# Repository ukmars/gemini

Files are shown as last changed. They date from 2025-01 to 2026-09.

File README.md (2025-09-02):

# Overview

Here is the UKMARS repository for our Gemini Micromouse. A robot capable of competing in our half size line following, Full Size Wall following and Full Size Maze Solving competitions. 

The Gemini robot is a second revision of the clubs first robot UKMARSBOT https://github.com/ukmars/ukmarsbot
Gemini has been designed so that the core microprocessor can be changed without having to change the chassis or sensor configuration. This has been done with what we call a mezzanine board. This "Mez" board connects the microprocessor to the chassis and the sensors.

At present the robot has been designed around the Raspberry Pi Pico (w)  to facilitate the use of MicroPython as a control language for the robot. This is taught is schools and allows schools to use the robot as part of their teaching aid. The Pico allows for other languages as well with the first alternative being C.

It is possible to build a Gemini robot using all commercially available parts.

In the future we hope to offer different Mez boards to allow a range of microcontrollers to be used. We are always looking for help from the community. So if you would like to design a mez board for a different microcontroller please get in touch.

This repo will contain all you need in order to build your own Gemini robot and get ready to compete in our competitions 

The groups website can be found https://ukmars.org/

A step by step build guide can currently be found https://ukmars.org/projects/gemini/

This "main" repo contains details relevant to the very latest PCB's that have been produced and distributed to schools and group members.  If you know you have a different version board than the latest (unlikely) you can find relevant KiCad documents in a release relating to your board. You will see a link to this on the right of this message

If you have found your way here without knowing about the UKMARS group, welcome. Becoming a member of UKMARS automatically gets you a set of PCB to build your own Gemini robot. All you have to do is source the parts and build.

# Technology details

All of the boards have been designed using the latest version 8 release of KiCad. They may get upgraded to version 9 but this is not a priority at the moment and the automations we have in place are not  compatible with v9.

You do not need KiCad installed in order to view the boards or the schematics

# Build details

The docs folder contains schematics, PCB renders and BOM lists. These are built directly from the KiCad and the component choices listed in the schematic represents the groups default choice of component. They are not necessarily the only option and builders are free to change the spec of components if they feel they have suitable technical knowledge to do so.
In addition to the components listed in the \docs\all_projects_bom.csv you will also need the following components to build a mouse.

# Supplier details

## Components

The following is a list of recommended UK supplier for the passive components of the board. Due to shipping costs we do recommend trying to source all passive components from one supplier if at all possible.

RSonline - https://uk.rs-online.com/web/

Rapid electronics - https://www.rapidonline.com/

Farnell - https://uk.farnell.com/

## Robot bits, Microprocessors and other

The following sites can be used to find the components not available from the above suppliers

https://thepihut.com/

https://shop.pimoroni.com/ - Motors and Encoders

https://www.amazon.co.uk/ - good for batteries and the DC motor controller

## Mechanical Parts not in the BOM

| Item | Description | part numbers and supplier options |
| --- | --- | --- |
| Encoders and encoder cables | These can be ordered along side the motor so you might have already looked at these<br>You will need two 6 pin 1mm pitch JST-SH cables to connect the motor encoder to the main board. An adaptor is used to convert the JST-SH cable to 2.54 pitch to connect it to J1 and J2 | |
| Encoder adapter board | This board converts JST-SH to 2.54 pins.<br>This does make soldering of the robot easier.<br>You can omit this part if you are comfortable soldering wires from a JST-SH cable direct to the chassis board | https://thepihut.com/products/breakout-for-6-pin-jst-sh-style-connector-side-entry |
| JST_SH cables | These cables connect the motor encoder to the chassis.<br><br>If you are comfortable soldering small cables direct to the chassis then you can use the second option. You DO NOT need the JST-SH adaptor board if you solder the wires direct to the chassis. This option is for experienced builders only as it increases the risk of problems with motors and/or encoders reading being reversed.  | https://thepihut.com/products/jst-gh-1-25mm-pitch-6-pin-cable-100mm-long<br><br><br>https://amzn.eu/d/hsau12j |
| Wheels and Tyres | Pololu Wheel 32×7mm Pair available in black or white or you could 3D print some and use O rings for tyres | Pi Hut SKU: POL-1087 or SKU: POL-1088<br><br>https://thepihut.com/products/pololu-wheel-32x7mm-pair-black |
| Motor Mounts | You need 2 motor mounts. They can be 3D printed if you have the capability or you can buy the Polulo ones.<br><br>3D print models can be found in the \mechanical folder. GeminiN20MotorMount.STL - Print upside down | Pi Hut code SKU: POL-989<br><br>https://thepihut.com/products/pololu-micro-metal-gearmotor-bracket-pair-black |
| Battery and connector | The battery should be a PP3 9Volt block Lithium Ion rechargeable one with micro USB charging socket and ideally charge level LEDs on the side.<br>Ideally 1200mAH capacity or greater | https://amzn.eu/d/i8hoP5S<br><br>https://amzn.eu/d/cmckSHt<br><br>Rapid Online Order Code: 18-0092 |
| Nuts and bolts | If you are using 3D printed mounts which have 3mm holes in them you need 4 M3 x 30mm flat head polyamide bolts. Pack of M3 polyamide nuts 8 required<br><br>M3 x 10mm plastic spacers or 10mm piece of plastic tubing<br><br>Ebay is a good place to order small quantities of M3 hardware | Rapid Online Order Code: 51-3852<br><br>Rapid-Online Order Code: 51-3437<br><br>https://www.ebay.co.uk/str/kaysfasteners<br><br> |
| Stand Offs | Used for mounting connecting the sensor and mez board to the chassis<br><br>Lots of ways to do this but a pack of standoff's makes this simple.<br><br>A nylon screw and nut can be used as a skid | https://amzn.eu/d/eMlVNY3<br><br> |
|Screen|Not required, but a screen can be helpful. The important thing with a screen is the pin order which needs to be Gnd, Vcc, SCL, SDA left to right. Other screens can be used but will require custom connectors <br> *Warning* The screens available from Pimoroni can be used but their GND and Vcc pins are reversed when compared to the mez board connector. EXTREME care needs to be taken if wiring these|https://a.aliexpress.com/_EJEPBEO <br> https://amzn.eu/d/ffaTN75 

> All of the options here are what UKMARS believe to be the best starting options for schools and new builders. It does not represent the only options available. If you have suitable experience and knowledge feel free to swap components as you see fit. If you do deviate from the build guide and/or suggested components please make sure to mention this if you encounter problems.

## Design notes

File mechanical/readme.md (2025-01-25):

# Project Gemini - Mechanical Design

Here you will find parts models, drawings and descriptions relating ot the mechanical design of the Gemni robot.

This covers the physical layout and arrangement of the major components including the PCBs that make up the main chassis, the processor carrier, sensor boards, drive components and battery.

Something like this perhaps -though with less wood.

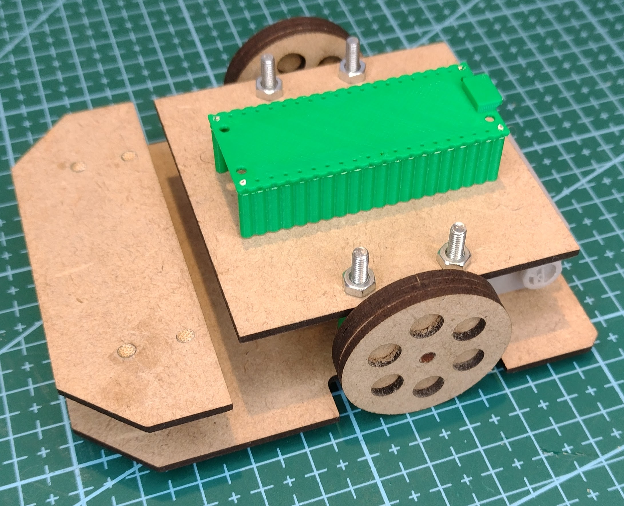
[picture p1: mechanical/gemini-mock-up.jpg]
gemini


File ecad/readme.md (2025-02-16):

# ECAD

Here you will find ECAD design files and resources such as part and footprint libraries.

The project will use KiCAD V8.0.x for all Schematic capture and PCB design.

Part datasheets will be stored in a separate folder.

Kicad models for the pico where found [here](https://github.com/ncarandini/KiCad-RP-Pico)
Install instructions [here](https://github.com/ncarandini/KiCad-RP-Pico/blob/main/Install%20instructions.md)

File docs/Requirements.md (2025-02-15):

# Requirements and Design Choices for Gemini

## Brief

This document states the core requirements and end offering that Gemini will provide.

## Board connections

| Name | Pin  | A/D | Direction | Function |
|---|---|-----|---|---|
| **Connector 1 on Chassis to Mezzanine** |  |  |  |  |
| 5v | Con1 | 0 | Pwr Out | +5v regulated supply provided by chassis |
| Gnd | Con1 | 1 | Pwr Out | Gnd provided by chassis |
| LMTR1 | Con1 | 2 D | In | Left motor input 1 to bridge |
| LMTR2 | Con1 | 3 D | In | Left motor input 2 to bridge |
| RMTR1 | Con1 | 4 D | In | Right motor input 1 to bridge |
| RMTR2 | Con1 | 5 D | In | Right motor input 2 to bridge |
| **Connector 2 on Chassis to Mezzanine** |  |  |  |  |
| LQA | Con2 | 0 D | Out | Left quadrature encoder channel A |
| LQB | Con2 | 1 D | Out | Left quadrature encoder channel B |
| RQA | Con2 | 2 D | Out | Right quadrature encoder channel A |
| RQB | Con2 | 3 D | Out | Right quadrature encoder channel B |
| 3v3 | Con2 | 4 A | Pwr In | 3V3 regulated supply provided by mezzanine |
| Vbatt | Con2 | 5 A | Pwr Out | Battery voltage supply after polarity protection |
| **Connector 3 on Mezzanine to Sensor Board** |  |  |  |  |
| Vemit | Con3 | 0 | Pwr Out | Power supply for sensor emitters, designers choice from 5v, Vbatt or 3v3 |
| Gnd | Con3 | 1 | Pwr Out | Gnd routed from chassis |
| 3v3 | Con3 | 4 | Pwr Out | 3V3 regulated supply provided by mezzanine |
| SEN0DIO | Con3 | 5 D | In/Out | Digital I/O line 0 for sensors |
| SEN1DIO | Con3 | 6 D | In/Out | Digital I/O line 1 for sensors |
| SEN2DIO | Con3 | 7 D | In/Out | Digital I/O line 2 for sensors |
| SEN3DIO | Con3 | 8 D | In/Out | Digital I/O line 3 for sensors |
| SEN4DIO | Con3 | 9 D | In/Out | Digital I/O line 4 for sensors |
| SEN0AIP | Con3 | 10 A | In | Analogue input for sensor 0 |
| SEN1AIP | Con3 | 11 A | In | Analogue input for sensor 1 |
| SEN2AIP | Con3 | 12 A | In | Analogue input for sensor 2 |
| SEN3AIP | Con3 | 13 A | In | Analogue input for sensor 3 |
| SEN4AIP | Con3 | 14 A | In | Analogue input for sensor 4 |
| SEN5AIP | Con3 | 15 A | In | Analogue input for sensor 5 |
| SDA | Con3 | 14 D | In/Out | I2C Serial Data |
| SCL | Con3 | 15 D | In/Out | I2C Serial Clock |

## Main board

Will be the same size and dimensions of UKMARSBOT

## Processor Support

The primary Processor with be the Raspberry Pi RP2040, other processors can be supported with additional mezanine boards, the development of these boards is for robot builders to pursue.

## Mezzanine boards

Initially we will be designing a Mezzanine board for the PiPico/PiPicoW

Meazanine boards will achieve connection with the main chassis board with 20mm extented male headers. 0ptionally stackable female headers from the chassis board can be used with standard male headers on the mezanine board.
The mezanine board will be mounted on the rearmost pair of motor bracket bolts and the rearmost pair of sensor mounting bolts.
## Sensors

### Wall Sensor

### Line Sensor

## Motors

N20 extended motor shaft DC motors with side mount encoders. Gear ratios to be selected by the builder. Recommended ratios 50:1, 30:1 or 20:1. Higher ratios give better resolution and easier control, lower ratios give highr top speed.

[Motor and Encoders](https://shop.pimoroni.com/products/micro-metal-motor-encoder?variant=39888423354451)
or 
https://shop.pimoroni.com/products/micro-metal-motor-encoder?variant=39888423354451

The above encoders are preferred as they can route the cable forwards without adding height to the motor assembly. Other encoders with cables emerging at the top may fit withing the headroom above the motor, builders will need to confirm this if choosing alternative encoders.
The connection to the encoders are JST-SH, if possible pads for corresponding JST-SH sockets will be included in the chassis board. 0.1inch x 6 connectors will be included on the chassis board. 

## Motor Controller
We have decided to use the DRV8833 chipset on a Switch/HW-627 module board which available from multiple suppliers on Amazon or eBay.
Example supplier (no recommendation) https://www.ebay.co.uk/itm/285548428267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
Example supplier (no recommendation) https://www.ebay.co.uk/itm/195060438441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

Found [here](https://www.amazon.co.uk/dp/B07ML2RDNY) as well

Nice article explaining how to wire up [drv8833-arduino-tutorial](https://lastminuteengineers.com/drv8833-arduino-tutorial/)

## Motor Mounts
Pololu motor mounts or equivalent can be used. 3d Printed mounts will offer a better solution using standard M3 or M2.5 bolts with standoffs to mount the mezanine board.

## Wheels and Tyres
Standard 32mm Pololu wheels and tyres or equivalents will be used https://thepihut.com/products/pololu-wheel-32x7mm-pair-black

## Batteries

The design will accommodate a PP3 battery form factor. Builders may use any PP3 battery they prefer, or any other battery that will fit withing the form factor of a PP3 battery and presents a voltage no greater than 9v.
The battery connection to the chassis board will be 0.1inch x2. A polarised connector can be used but is not mandatory so a polarity protection diode is required on the chassis board.

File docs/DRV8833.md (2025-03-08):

# The DRV8833 Motor Driver

The chosen driver carrier is commonly available. It loks like this:



## SLEEP input

The driver chip has a pin called nSLEEP. On these cheap carriers, that pin is connected to a pin usually called 'EEP'. I guess they ran out of space.

From the perspective of the driver chip, if this pin is left open, it is pulled down by an internal resistor and the chip will be in sleep mode. That is, you will not get any outputs to the motors.

To enable the driver, the nSLEEP pin must be pulled up to the motor Voltage, $V_M$.

BUT...

There are many version of  the carrier. They have slightly different markings and they may, or may not, pull up the nSLEEP pin. This picture, from a random AliExpress vendor shows a jumper on the rear. It clearly shows hat the jumper must be bridged to enable the outputs. There is a 47k resisor on the board that performs this function when the jumper is bridged.


Apparently though, there are boards that have this jumper already bridged on the board so the outputs are always active.

Note that, if you look at boards from Pololu and Adafruit, this pin may, or may not already be pulled high. The Pololu carrier puls it high, the Adafruit carrier does not:

 - Pololu: https://www.pololu.com/product/2130
 - Adafruit: https://learn.adafruit.com/assets/36870

To be sure  the motor drive is enabled, pull the nSleep ('EEP) pin high with a 47k resistor connected to the motor supply.

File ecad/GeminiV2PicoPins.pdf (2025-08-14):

## UKMARS Gemini V2 PiPico Pin assignements

### Chassis and Mezzanine Pins

Pico GPIO | Mezz Net ID | Used on | Device | Device name | Description
| 0 GPIO00 | Mezz | J2-2 | Breakout connector | UART0-TX for bluetooth or GPIO pin
| 1 GPIO01 | Mezz | J2-3 | Breakout connector | UART0-RX for bluetooth or GPIO pin
| 2 LMTR1 | Chassis | U1-7 | DRV8833 motor controller | Left motor control signal 1
| 3 LMTR2 | Chassis | U1-8 | DRV8833 motor controller | Left motor control signal 2
| 4 RMTR1 | Chassis | U1-11 | DRV8833 motor controller | Right motor control signal 1
| 5 RMTR2 | Chassis | U1-12 | DRV8833 motor controller | Right motor control signal 2
| 6 RQA | Chassis | J2-3 | Right motor quadrature encoder | Signal A
| 7 RQB | Chassis | J2-2 | Right motor quadrature encoder | Signal B
| 8 LQA | Chassis | J1-3 | Left motor quadrature encoder | Signal A
| 9 LQB | Chassis | J2-2 | Left motor quadrature encoder | Signal B
| 10 GPIO10 | Mezz | J5-4 | Breakout connector | I2C1-SDA for display or GPIO pin
| 11 GPIO11 | Mezz | J5-3 | Breakout connector | I2C1-SCL for display or GPIO pin
| 12 GPIO12 | Mezz | D1 | Indicator LED | Left side
| 13 GPIO13 | Mezz | D2 | Indicator LED | Right side
| 14 GPIO14 | Mezz | SW2 | Pushbutton | Right side
| 15 GPIO15 | Mezz | SW1 | Pushbutton | Left side

### Line Sensor Pins

Pico GPIO | Mezz Net ID | Used on | Device | Device name | Description
| 16 SDA | Line Sensor | Not used
| 17 SCL | Line Sensor | Not used
| 18 SEN4DIO | Line Sensor | Q6 | BC337-40 | Radius emitter driver
| 19 SEN3DIO | Line Sensor | D6 | Indicator LED | S/F right side indicator
| 20 SEN2DIO | Line Sensor | D5 | Indicator LED | Line central indicator
| 21 SEN1DIO | Line Sensor | D4 | Indicator LED | Radius left side indicator
| 22 SEN0DIO | Line Sensor | Q1 | BC337-40 | Line and start/finish emitter driver
| 26 SEN2AIP | Line Sensor | Q4 | BPW85C | Line right side detector
| 27 SEN1AIP | Line Sensor | Q2 and Q5 | BPW85C | Radius and Start/finish detectors
| 28 SEN0AIP | Line Sensor | Q3 | BPW85C | Line left side detector
Not available | SEN3AIP | Not available
Not available | SEN4AIP | Not available
Not available | SEN5AIP | Not available

Page 1 of 2

### Wall Sensor Pins

Pico GPIO | Mezz Net ID | Used on | Device | Device name | Description
| 16 SDA | Wall Sensor | Not used
| 17 SCL | Wall Sensor | Not used
| 18 SEN4DIO | Wall Sensor | D3 | Indicator LED | Right side indicator
| 19 SEN3DIO | Wall Sensor | D2 | Indicator LED | Central (to the right) indicator
| 20 SEN2DIO | Wall Sensor | D1 | Indicator LED | Left side indicator
| 21 SEN1DIO | Wall Sensor | Q2 | BC337-40 | Driver for diagonal emitters
| 22 SEN0DIO | Wall Sensor | Q1 | BC337-40 | Driver for front emitter
| 26 SEN2AIP | Wall Sensor | RDPD1 | BPW85C | Right diagonal detector
| 27 SEN1AIP | Wall Sensor | FPD1 | BPW85C | Front detector
| 28 SEN0AIP | Wall Sensor | LDPD1 | BPW85C | Right diagonal detector
Not available | SEN3AIP | Not available
Not available | SEN4AIP | Not available
Not available | SEN5AIP | Not available

Page 2 of 2

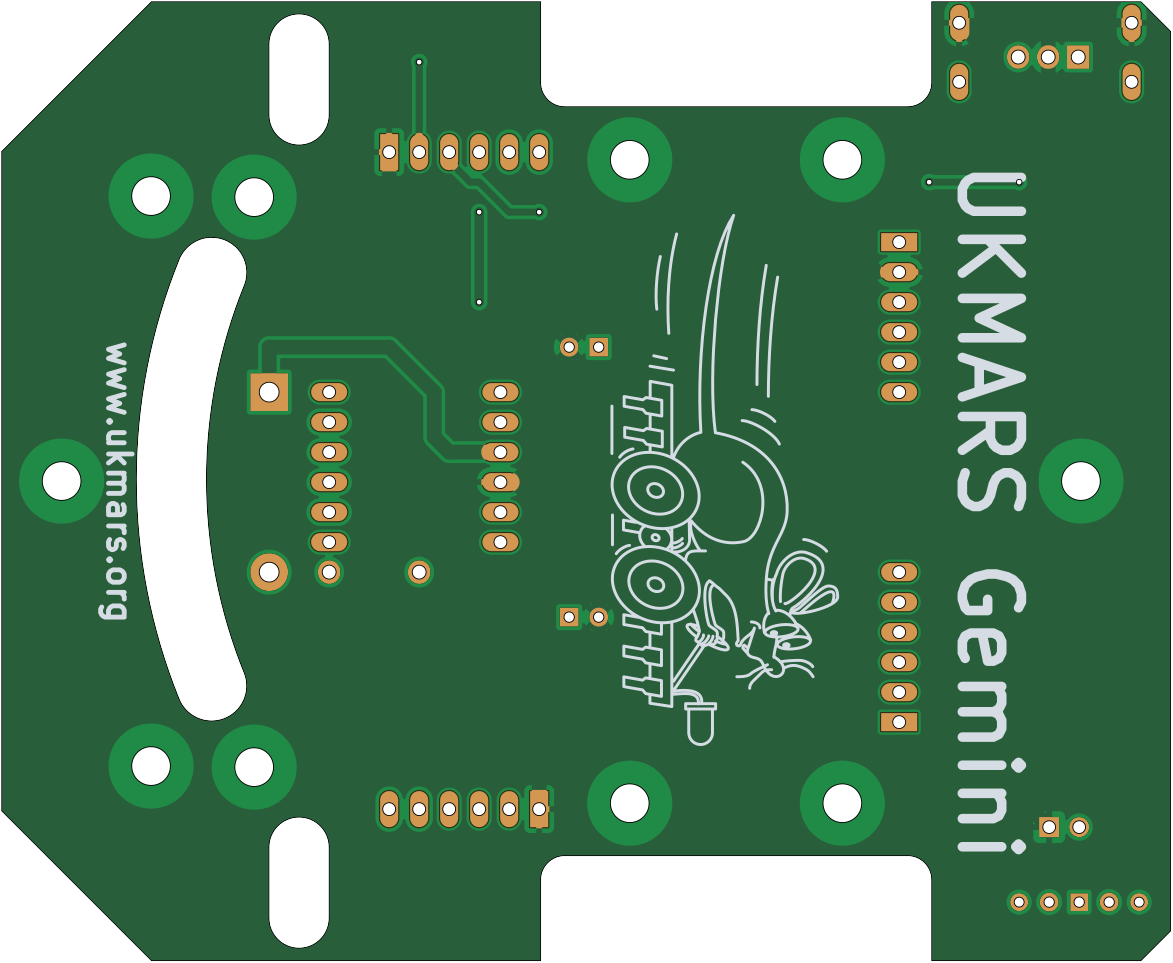
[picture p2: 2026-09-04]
docs/UKMARSBOT_RP2040Chassis/UKMARSBOT_RP2040Chassis_board_bottom.png

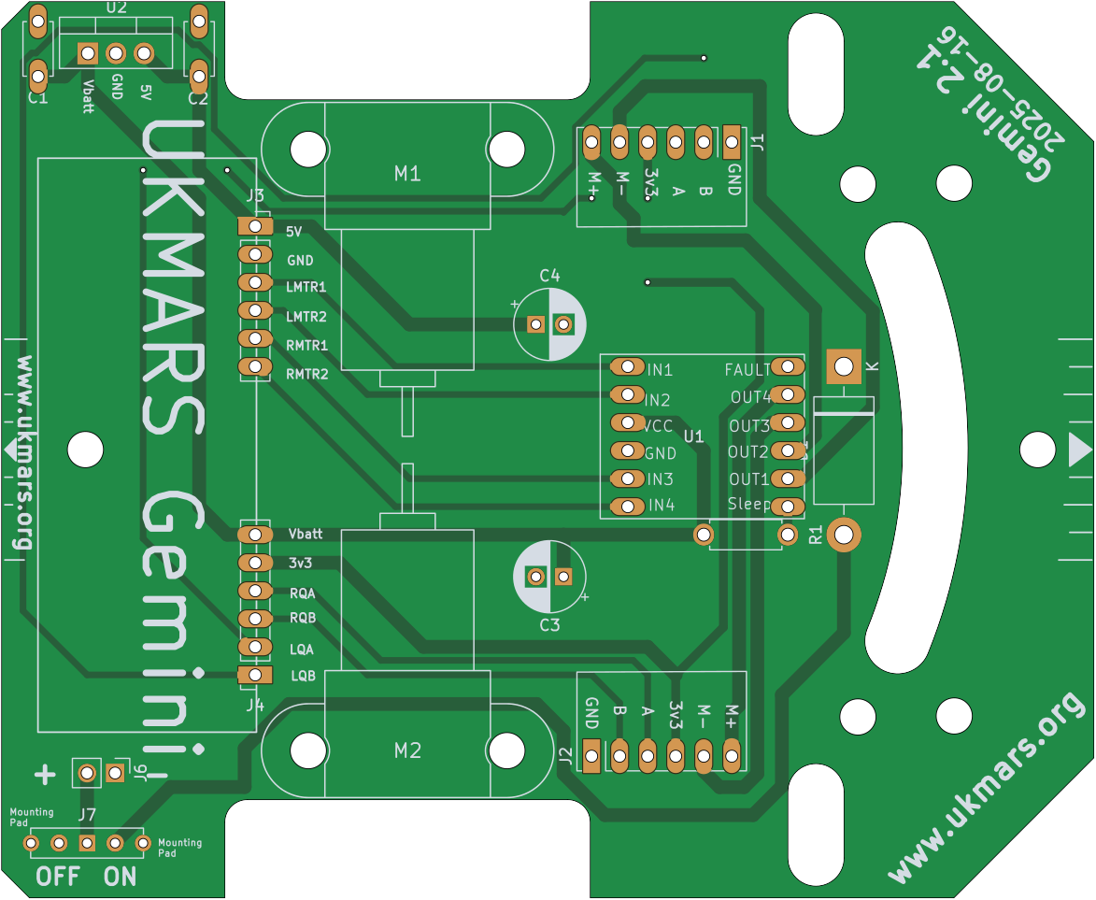
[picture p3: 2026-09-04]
docs/UKMARSBOT_RP2040Chassis/UKMARSBOT_RP2040Chassis_board_top.png

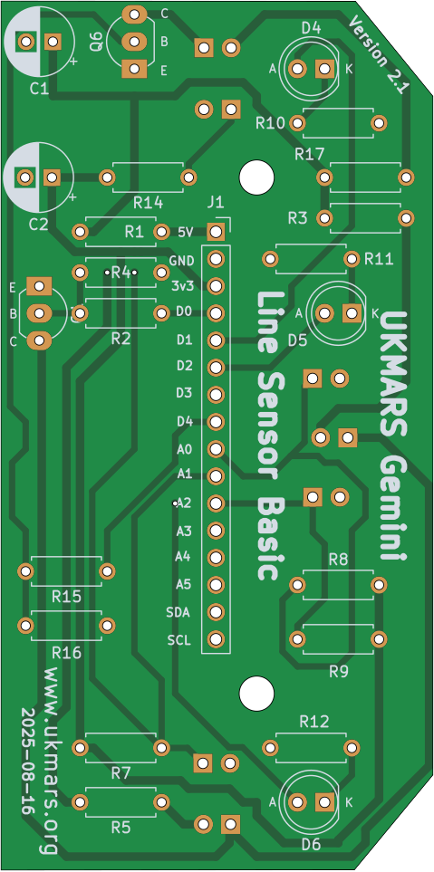
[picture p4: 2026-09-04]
docs/UKMARSBOT_LineSensorBasic/UKMARSBOT_LineSensorBasic_board_top.png

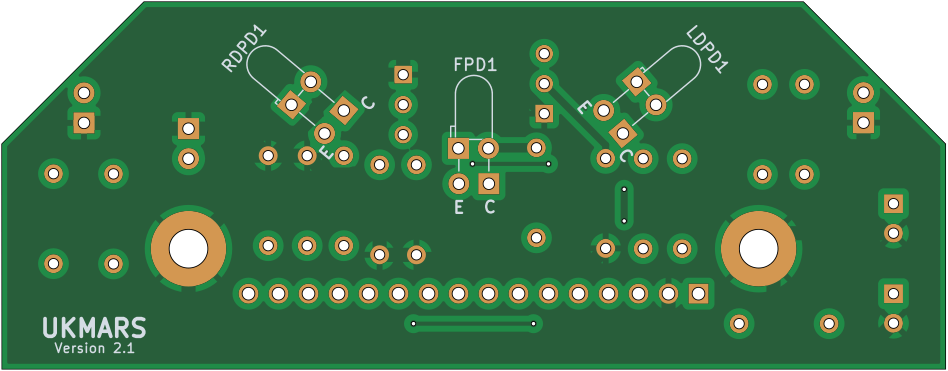
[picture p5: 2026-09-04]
docs/UKMARSBOT_RP2040Wall-Sensor-Basic/UKMARSBOT_RP2040Wall-Sensor-Basic_board_bottom.png

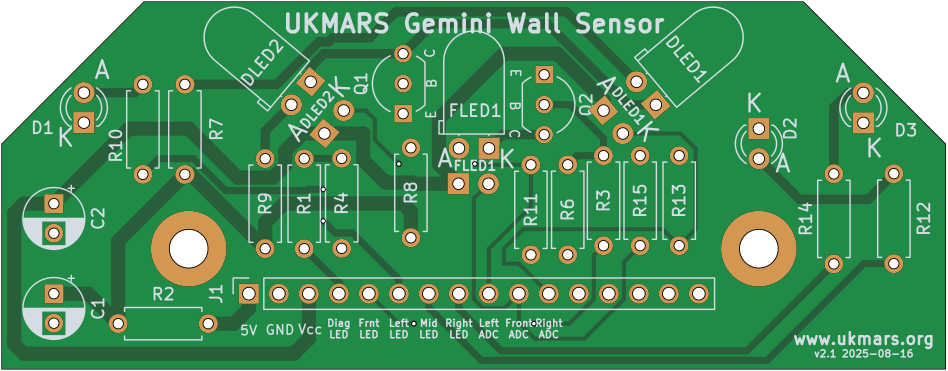
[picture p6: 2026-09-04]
docs/UKMARSBOT_RP2040Wall-Sensor-Basic/UKMARSBOT_RP2040Wall-Sensor-Basic_board_top.png

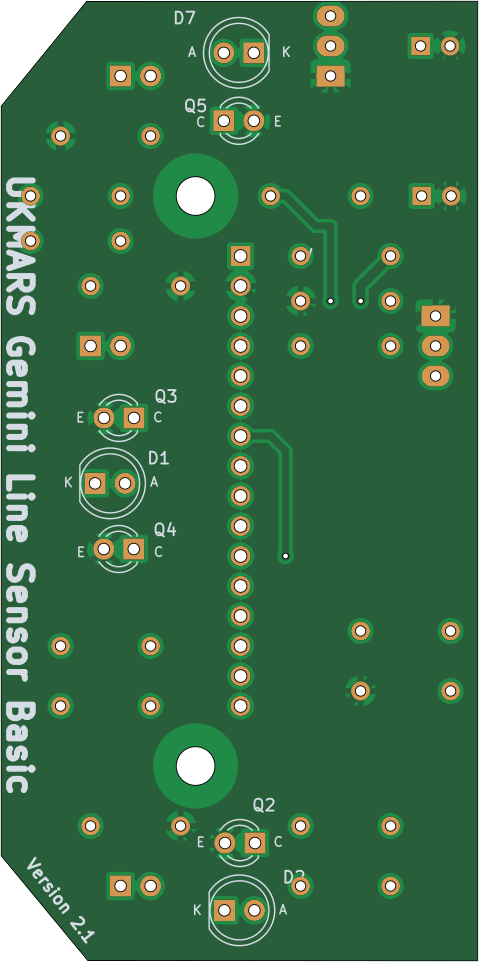
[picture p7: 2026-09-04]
docs/UKMARSBOT_LineSensorBasic/UKMARSBOT_LineSensorBasic_board_bottom.png

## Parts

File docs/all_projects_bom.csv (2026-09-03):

Project | Reference | Value | Qty | Note | Description | RSONLINE | RAPID
UKMARSBOT_LineSensorBasic | C1 C2 | 100uF | 2 |  | Polarized capacitor | 176-3779 | 11-4109
UKMARSBOT_LineSensorBasic | D1 D2 D7 | TLCR5800 | 3 |  |  | 818-7540 | 55-0066
UKMARSBOT_LineSensorBasic | D4 | Radius | 1 |  |  | "228-6004 or 228-5562 or 713-3974 or 813-4845" | 56-0400
UKMARSBOT_LineSensorBasic | D5 | Line | 1 |  |  | "228-6004 or 228-5562 or 713-3974 or 813-4845" | 56-0405
UKMARSBOT_LineSensorBasic | D6 | S/Finish | 1 |  |  | "228-6004 or 228-5562 or 713-3974 or 813-4845" | 56-0410
UKMARSBOT_LineSensorBasic | J1 | Conn_01x16 | 1 | https://uk.rs-online.com/web/p/pcb-sockets/6816820 Need to be cut down | Generic connector, single row, 01x16, script generated (kicad-library-utils/schlib/autogen/connector/) | 681-6820 | 19-0087
UKMARSBOT_LineSensorBasic | Q1 Q6 | BC337-40 | 2 |  |  | 671-1119 | 50-3113
UKMARSBOT_LineSensorBasic | Q2 Q3 Q4 Q5 | BPW85C | 4 |  |  | 815-1263
UKMARSBOT_LineSensorBasic | R1 | 47R | 1 |  | Resistor | 707-8817 | 62-0334
UKMARSBOT_LineSensorBasic | R2 R15 | 390R | 2 |  |  | 707-7634 | 62-0360
UKMARSBOT_LineSensorBasic | R3 R5 R17 | 10R | 3 |  |  | 707-8580 | 62-0326
UKMARSBOT_LineSensorBasic | R4 R16 | 10K | 2 |  |  | 707-7745 | 62-0394
UKMARSBOT_LineSensorBasic | R7 R8 R9 R10 R11 R12 R14 | 680R | 7 |  |  | 707-8211 | 64-0068
UKMARSBOT_RP2040Chassis | BT1 | 9v Battery | 1 |  | PP3 9v Battery
UKMARSBOT_RP2040Chassis | C1 | 0.22uF | 1 | Maximum height is 10mm | Unpolarized capacitor | 194-0629 | 11-3449
UKMARSBOT_RP2040Chassis | C2 | 0.1uF | 1 | Maximum height is 10mm | Unpolarized capacitor | 538-1433 | 11-3442
UKMARSBOT_RP2040Chassis | C3 C4 | 100uF, 16V | 2 | Maximum height is 10mm |  | 176-3779 176-3779 | 11-4109
UKMARSBOT_RP2040Chassis | D1 | 1N5401 | 1 | Polarity protection diode |  | 628-9451
UKMARSBOT_RP2040Chassis | J1 J2 | Pololu Item #4772 | 2 | 6 pin 0.1" breakout 6 pin header, 0.1", male | Single row, 01x06, JST-SH breakout |  | 22-0795
UKMARSBOT_RP2040Chassis | J3 J4 J6 J7 | Conn_01x06 | 4 | Might be easier and cheaper to just cut from bigger lengths 0.1" pitch, polarised, any type | https://uk.rs-online.com/web/p/pcb-headers/6812994 | 681-2994 | 01-5723 08-5765 78-0566
UKMARSBOT_RP2040Chassis | M1 M2 | N20 MOTOR | 2 | Sidways or regular would work for starting out 50:1 gearbox is recommended commercial mounts need bushing for screws | https://shop.pimoroni.com/products/micro-metal-motor-encoder?variant=39888423321683 | NA
UKMARSBOT_RP2040Chassis | R1 | 47K | 1 |  | Resistor | 707-8369 | 62-0410
UKMARSBOT_RP2040Chassis | U1 | DVR8833_DC_Controller | 1 |  | DC Motor Controller https://amzn.eu/d/csv7cRr as an option
UKMARSBOT_RP2040Chassis | U2 | LM7805_TO220 | 1 |  | Positive 1A 35V Linear Regulator, Fixed Output 5V, TO-220 | 793-1346
UKMARSBOT_RP2040Mezzanine | D1 D2 | LED | 2 |  | Light emitting diode | "228-6004 or 228-5562 or 713-3974 or 813-4845" | 56-0400 and 56-0405
UKMARSBOT_RP2040Mezzanine | J1 J2 J3 J4 J5 | Conn_01x16 | 5 | Might be easier and cheaper to just cut from bigger lengths Cut from a bigger strip of 2.54 header | Generic connector, single row, 01x16, script generated (kicad-library-utils/schlib/autogen/connector/) Generic connector, single row, 01x06, script generated (kicad-library-utils/schlib/autogen/connector/) Generic connector, single row, 01x04, script generated | 681-3007 681-2994 | 08-7948 01-5723 01-5835
UKMARSBOT_RP2040Mezzanine | R1 R2 | 680R | 2 |  | Resistor | 707-8211 | 64-0068
UKMARSBOT_RP2040Mezzanine | SW1 SW2 SW3 | TACT_SW | 3 |  | TACT switch 6mm 4.5mm | 479-1390P | 78-3821
UKMARSBOT_RP2040Mezzanine | U1 | Pico | 1 |  |  |  | 08-7949 and 75-1230
UKMARSBOT_RP2040Wall-Sensor-Basic | C1 C2 | 100uF, 16v | 2 |  | Unpolarized capacitor | 739-6799 | 11-4119
UKMARSBOT_RP2040Wall-Sensor-Basic | D1 D2 D3 | LED | 3 |  | Light emitting diode | "228-6004 or 228-5562 or 713-3974 or 813-4845" | 56-0400 or 56-0405 or 56-0410
UKMARSBOT_RP2040Wall-Sensor-Basic | DLED1 DLED2 FLED1 | TLCR5800 | 3 |  | Light emitting diode | 818-7540
UKMARSBOT_RP2040Wall-Sensor-Basic | FPD1 LDPD1 RDPD1 | BPW85C | 3 |  | Photodiode | 815-1263
UKMARSBOT_RP2040Wall-Sensor-Basic | J1 | Conn_01x16 | 1 | https://uk.rs-online.com/web/p/pcb-sockets/6816820 Can also be found on ebay slightly cheaper | Generic connector, single row, 01x16, script generated (kicad-library-utils/schlib/autogen/connector/) | 681-6820 | 19-0087
UKMARSBOT_RP2040Wall-Sensor-Basic | Q1 Q2 | BC337-40 | 2 |  | NPN transistor, emitter/base/collector | 671-1119 | 50-3113
UKMARSBOT_RP2040Wall-Sensor-Basic | R1 R3 | 390R | 2 |  | Resistor | 707-7634 | 62-0360
UKMARSBOT_RP2040Wall-Sensor-Basic | R10 R12 R14 | 680R | 3 |  | Resistor | 707-8211
UKMARSBOT_RP2040Wall-Sensor-Basic | R11 R13 | 2k2 | 2 |  | Resistor | 707-8255 | 62-0378
UKMARSBOT_RP2040Wall-Sensor-Basic | R15 | 1k8 | 1 |  | Resistor | 707-8675 | 62-0376
UKMARSBOT_RP2040Wall-Sensor-Basic | R2 | 33R | 1 |  | Resistor | 707-8805 | 62-0334
UKMARSBOT_RP2040Wall-Sensor-Basic | R4 R6 | 10K | 2 |  | Resistor | 707-7745 | 62-0394
UKMARSBOT_RP2040Wall-Sensor-Basic | R7 R8 R9 | 10R | 3 |  | Resistor | 707-8580 | 62-0326

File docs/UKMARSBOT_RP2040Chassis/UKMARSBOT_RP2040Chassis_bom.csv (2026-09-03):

Reference | Value | Qty | Note | Description | RSONLINE | RAPID
BT1 | 9v Battery | 1 |  | PP3 9v Battery
C2 | 0.1uF | 1 | Maximum height is 10mm | Unpolarized capacitor | 538-1433 | 11-3442
C1 | 0.22uF | 1 | Maximum height is 10mm | Unpolarized capacitor | 194-0629 | 11-3449
C3 C4 | 100uF, 16V | 2 | Maximum height is 10mm |  | 176-3779 176-3779 | 11-4109
D1 | 1N5401 | 1 | Polarity protection diode |  | 628-9451
J3 J4 J6 J7 | Conn_01x06 | 4 | Might be easier and cheaper to just cut from bigger lengths 0.1" pitch, polarised, any type | https://uk.rs-online.com/web/p/pcb-headers/6812994 | 681-2994 | 01-5723 08-5765 78-0566
J1 J2 | Pololu Item #4772 | 2 | 6 pin 0.1" breakout 6 pin header, 0.1", male | Single row, 01x06, JST-SH breakout |  | 22-0795
M1 M2 | N20 MOTOR | 2 | Sidways or regular would work for starting out 50:1 gearbox is recommended commercial mounts need bushing for screws | https://shop.pimoroni.com/products/micro-metal-motor-encoder?variant=39888423321683 | NA
R1 | 47K | 1 |  | Resistor | 707-8369 | 62-0410
U1 | DVR8833_DC_Controller | 1 |  | DC Motor Controller https://amzn.eu/d/csv7cRr as an option
U2 | LM7805_TO220 | 1 |  | Positive 1A 35V Linear Regulator, Fixed Output 5V, TO-220 | 793-1346

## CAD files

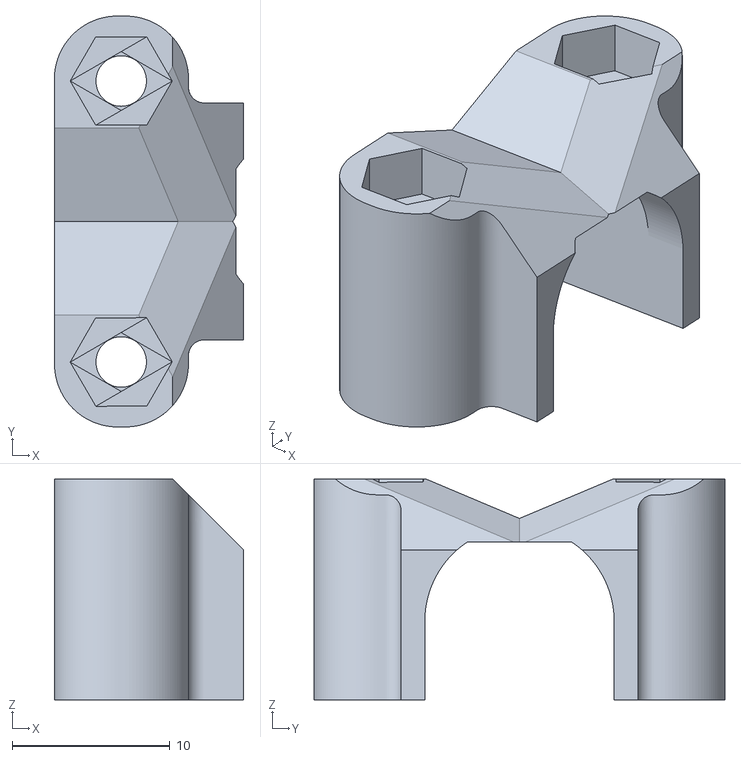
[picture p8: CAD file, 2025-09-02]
mechanical/GeminiN20MotorMount.stl
12.0 x 26.0 x 14.0

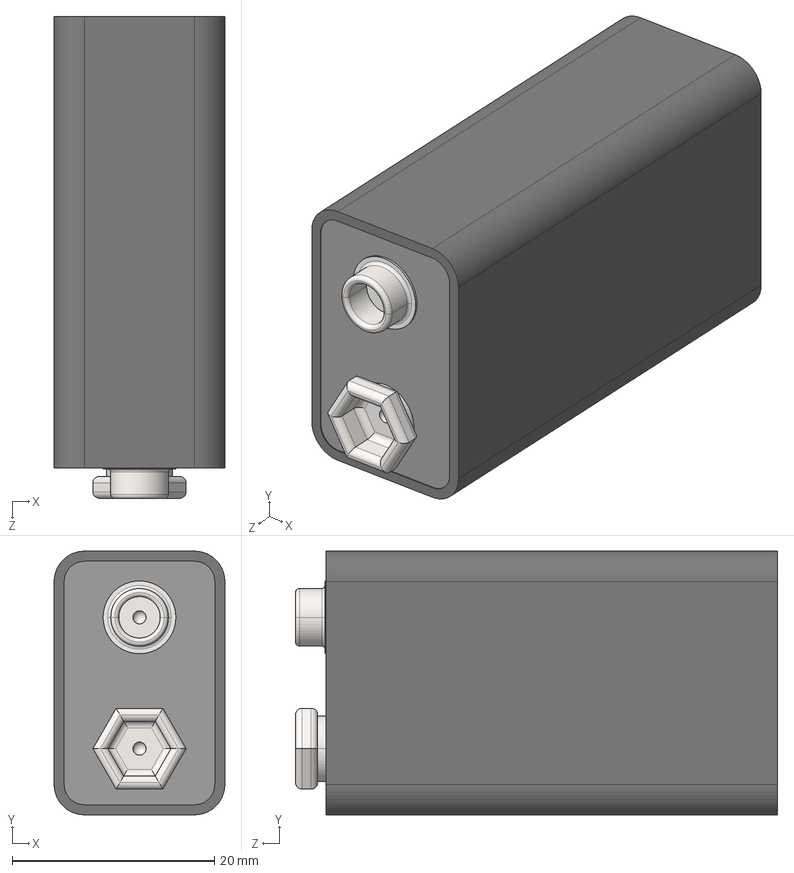
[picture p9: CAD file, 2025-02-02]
mechanical/Battery_9V.STEP
16.9 x 26.1 x 47.7 mm

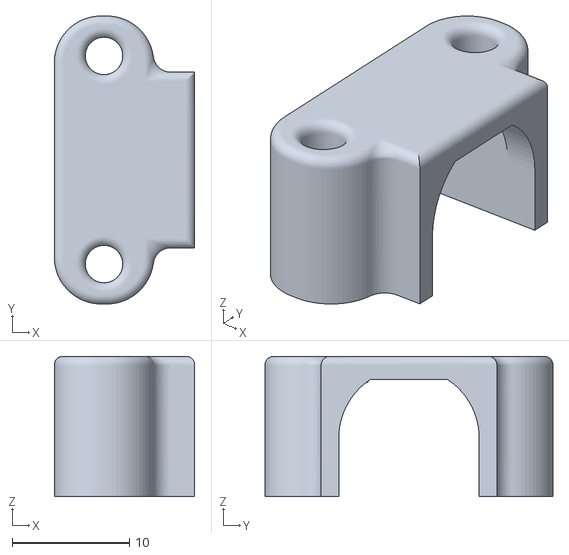
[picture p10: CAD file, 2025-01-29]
mechanical/motor-bracket.stl
12.0 x 24.6 x 12.0

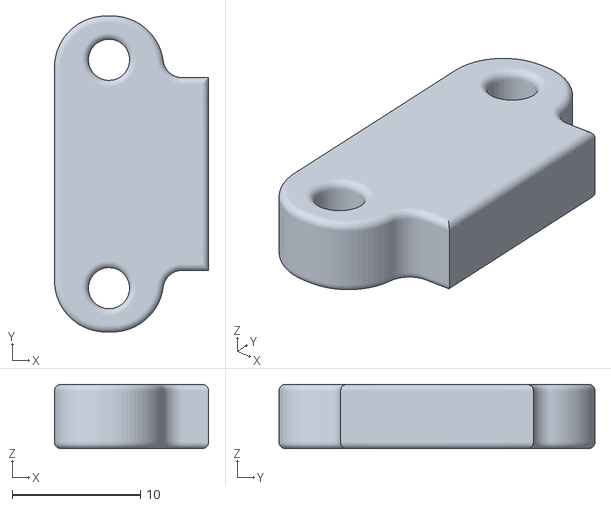
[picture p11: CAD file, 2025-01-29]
mechanical/motor-riser-5mm.stl
12.0 x 24.6 x 5.00

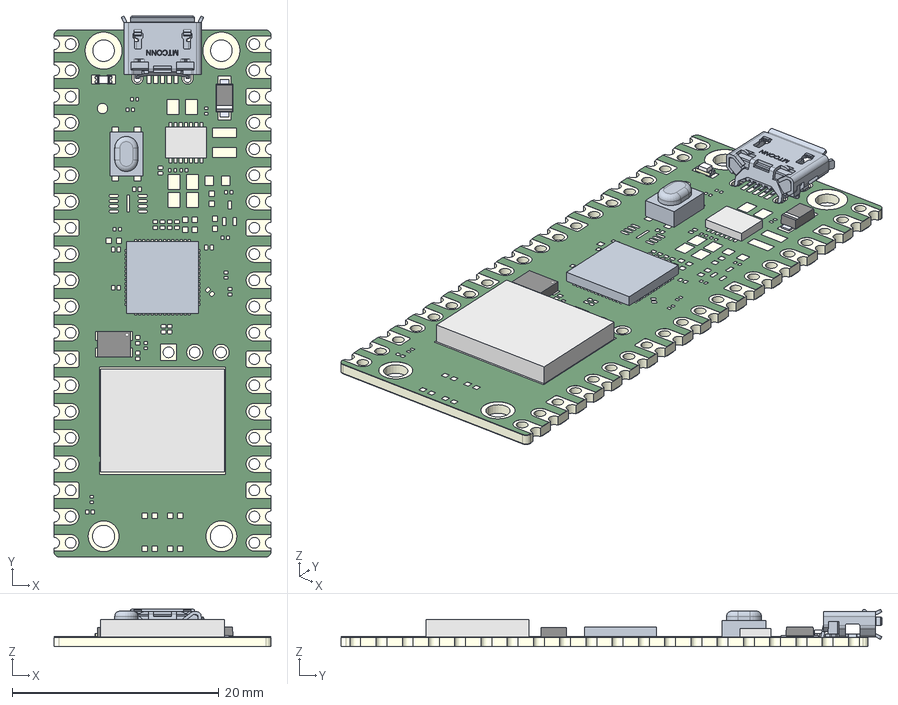
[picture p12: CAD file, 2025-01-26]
mechanical/RP2040-PICO-W.stp
21.0 x 52.4 x 3.66 mm
SOLDERMASK_TOP
Dielectric
SOLDERMASK_BOTTOM
AVAGO_QSM
FCI_10103594-0001LF
RF_SHIELD_PICOW
RPI_RP2040
RT-WDFN-14AL
SOD123FL
TONEPARTS_TP-1221U-K9K5325
XTAL320X250X100

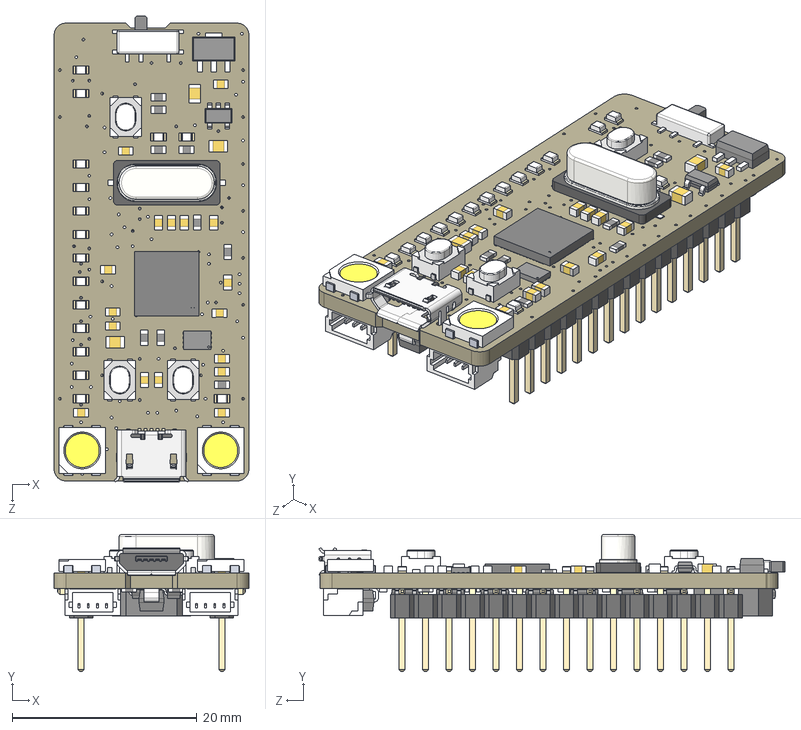
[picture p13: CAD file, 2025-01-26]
mechanical/MAKER-NANO-RP2040.STEP
21.1 x 14.8 x 50.4 mm
Board
JST-SM04B-SRSS-TB x 2
S-HDR-M1X15 x 2
USB-MICRO-B-REC
QFN-56
SOT-23-5
SOT-23 x 15
SOT-89-3
ThermalPin
PinsArrayLR
CCAP-1608 x 18
CCAP-2012 x 3
D-SMA
LED-1608 x 16
LED-5050-WS2812B x 2
R-1608 x 38
S-BUZZER-HXD-8530A-03627
SW-PB-KAN3246 x 3
SW-SLIDE-SPDT-SMD
XTAL-HC49UP

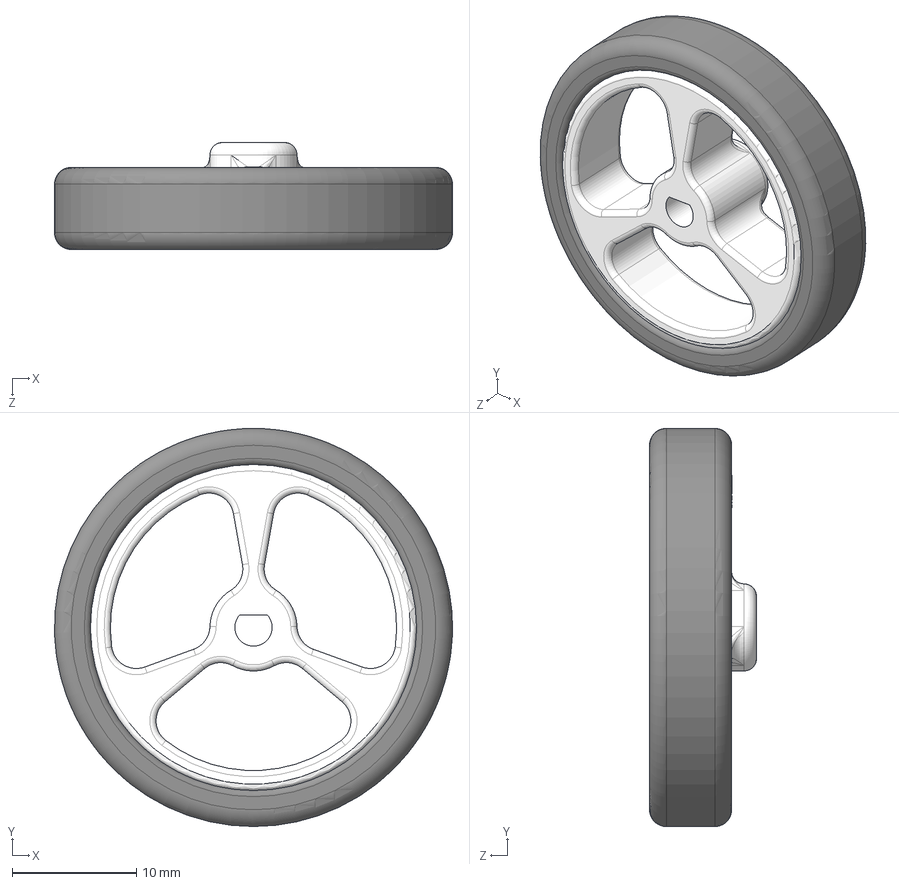
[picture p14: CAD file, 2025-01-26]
mechanical/pololu-wheel-32x7mm-white.step
32.0 x 32.0 x 8.60 mm

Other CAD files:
mechanical/pololu-wheel-32x7mm-black.step

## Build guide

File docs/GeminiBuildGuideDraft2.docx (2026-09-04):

# UKMARS GEMINI Build Guide

# 1 Introduction

GEMINI

GEMINI is a new robot based around the proven design principles of UKMARSBOT while adding the power of the Raspberry Pi Pico or Pi Pico W processor to allow programming in MicroPython.

Like the basic UKMARSBOT robot, this design is equally at home in the maze or on a line following track.

The 3-level design means that if you want to use an alternative MCU processor this can be done by just amending the top PCB for the new processor and fitting it to the remaining PCBs.

The design is completely Open Source and is fully described in these pages and the links within them. The design has been produced with KiCAD a free CAD CAM program. The best way to access reference material including this guide is to visit https://github.com/ukmars/gemini/

## 1.1 Where to get your Printed Circuit Boards (PCBs)

Gemini comprises 4 printed circuit boards (PCBs).

- a main chassis board hosting motors, battery and power
- a mezzanine board for the MCU processor and expansion slots
- a line sensor board for line following and drag racing
- a wall sensor board for wall following and maze solving

The main chassis board and the 2 sensor boards are common to all the different processors, but the mezzanine board is tailored to a specific processor module. The version described in this build guide has the mezzanine board designed for use with the Raspberry Pi Pico or Pico W processor board.

Members of UKMARS can obtain a copy of the 4 boards for free from the UKMARS Chairman. If you need more PCBs, or prefer to order your own boards, you can send a zipped copy of the Gerber files which can be downloaded from GitHub to your preferred PCB supplier (e.g. https://jlcpcb.com/ or www.pcbway.com) and they will ship the PCBs directly to you.

## 1.2 What’s in this Build Guide

This guide goes through the build process step by step:

Section 2 Tools and Components A list of the tools you will need together with where to find the parts needed to build a Gemini Robot

Section 3 Main Chassis – Buggy How to populate the main chassis PCB with the electronic components and connectors

Section 4 Fitting Encoders and Mounting Motors How to attach encoders to the motors, mount the motors and connecting them up

Section 5 Line Sensor Board How to populate the line sensor PCB with its electronic components,

Section 6 Wall Sensor Board How to populate the wall sensor PCB used for wall following and maze solving with its electronic components,

Section 7 Mezzanine Processor Board How to populate the mezzanine PCB with its processor and other electronic components

Section 8 Putting it all together How to connect the PCBs and mechanical parts together to make the complete system

Section 9 Testing, Coding and Further Reading How to test your robot and links to the design documents including: the main circuit diagrams and sample code.

Appendix A – Example Bill Of Materials (BOM) A sample list of all the components needed to build a Gemini robot

Appendix B – Resistor Colour Code Chart How to identify the value of a resistor from the colour bands on the body of the resistor

## 1.3 How to access reference and support documents

The easiest way to access all the designs, support documents and code examples is to visit out GitHub repo at https://github.com/ukmars/gemini/

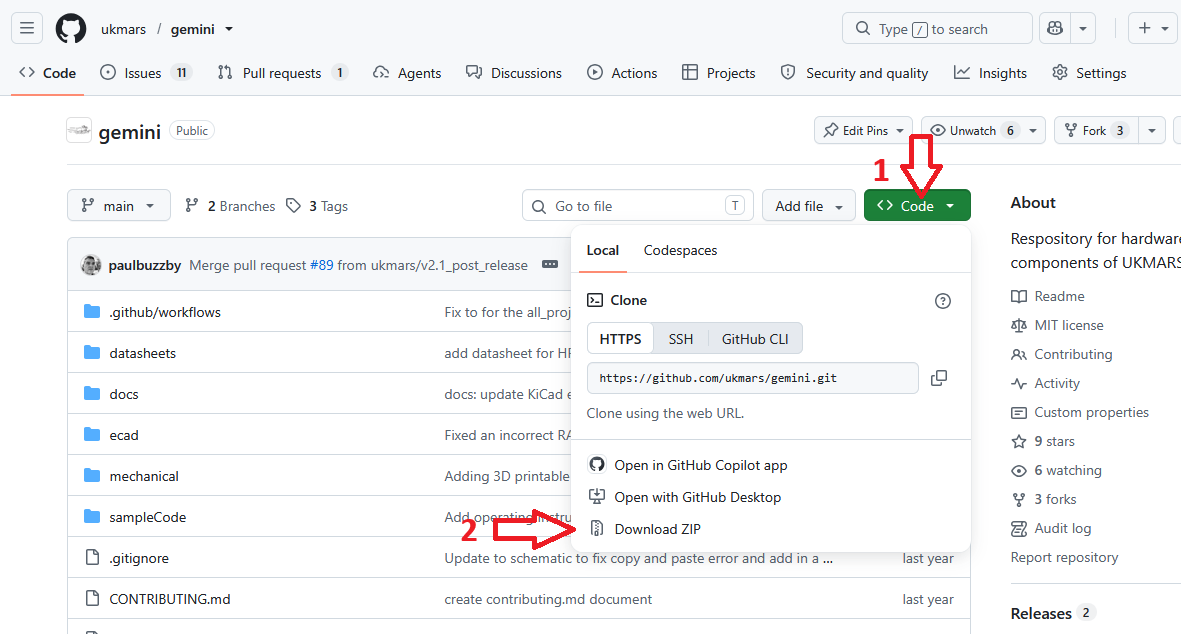
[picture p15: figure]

First click on the green button labelled “Code” then select “Download ZIP” from the drop down. A ZIP folder containing all the materials will be downloaded to your device and you can browse through the downloaded folders and files to find what you need. This build guide can be found in the “docs” folder of our repository.

If you are familiar with GitHub you can clone the repository to your device and ensure that you are kept up to date when items change.

## 1.4 Getting Started

Before you start building the GEMINI robot you will need to get yourself organised!

- read through this build guide and get familiar with the contents
- Have a look at the Tools and Components page and make a list of the tools and parts that you need to get.
- Where you have options, such as for motors, encoders and batteries, read the Choosing Motors, Choosing Batteries and Fitting Encoders pages to help you decide what specific items you want
- Identify suppliers and part numbers for the parts that you will order. Group them by supplier and get as many as you can from a few suppliers as this will reduce your postage costs. Don’t forget that you will only be able to get the main PCB and sensor PCBs from UKMARS unless you want to get these PCBs produced yourself. Remember that parts bought on EBay that are coming from abroad may take some weeks or longer to be delivered.
- Follow through this guide step by step to build your GEMINI robot

Throughout this guide if there is an optional alternative method or component the alternative is shown in italics. The intended design is always shown in normal text and the alternatives in italics should only be used where you are sure that they meet your needs.

# 2 Tools and Components

## 2.1 Tools

The robot is designed to be built with a limited set of tools.
You will need the following:

- A soldering iron with a small bit, plus solder
- A small pair of side cutters for clipping component leads and wires to length
- A small pair of pliers for holding parts and nuts while being tightened and optionally a long-nosed pair.
- Flat and cross head screwdrivers for tightening nuts and bolts
- A digital multi meter to measure voltages and resistance values. Typically, under £10 on ebay

## 2.2 Components

A list of all the components you will need is included in the Bill Of Materials(BOM) list that you will find in the “docs” folder in the repository. If you have downloaded the zip folder as described in section 1.3 How to access reference and support documents you will find the file “all_projects_bom.csv” in the “docs” folder or you can view it here https://github.com/ukmars/gemini/blob/main/docs/all_projects_bom.csv

The BOM includes item references for two major suppliers: Rapid Electronics https://www.rapidonline.com/ and RS Online https://uk.rs-online.com/web/. One of the design goals of GEMINI is to use widely available components. Components can be purchased from other suppliers as long as they meet the specifications in the design documents. The item references are included to help to identify which components need to be purchased. UKMARS does not endorse any specific supplier other suppliers such as https://uk.farnell.com/ are available.

An example of the BOM is included at Appendix A – Example Bill Of Materials (BOM) to this document and can be used for information. The latest definitive BOM is published here https://github.com/ukmars/gemini/blob/main/docs/all_projects_bom.csv

## 2.3 Choosing Motors

One of the key decisions that needs to be made is which motors to use. The robot is designed to use two N20 12mm micro gearmotors. These are widely available on Ebay and electronics and hobby robotics sites from £5 to £20 each.

### 2.3.1 The Best Choice for New Constructors

This section describes the choices that need to be made to select the best motor for your robot. If you are new to building robots and find all the choices a bit daunting it is recommended that you use a Pololu or Pimoroni 6-volt N20 gearmotor with extended back shaft and a gear ratio of either 20:1 or 30:1. If you can get a high-power version then that will be an advantage.

### 2.3.2 Encoders

Basic line following, wall following and drag racing can be achieved without encoders but if you want your robot to perform at the best level achievable or you aspire to maze solving, they will be needed. It is much better to fit the relatively cheap encoders in the initial build so that you can accurately measure speed and distance covered.

To fit encoders directly to the motors you need to buy the motors that have an extended back shaft out of the opposite side of the motor to the gearbox. This will reduce your range of available motors but if you search on the internet for “micro metal gearmotor extended back shaft” you should find suitable ones either on EBay or from suppliers such as Pimoroni or Pololu.

### 2.3.3 Gear Ratio

These N20 motors come in a very wide range of available gear ratios, from typically 5:1 to over 1000:1. A low gear ratio such as 10:1 will allow your robot to go faster, but it will be more difficult to control as you will have less torque available. The suggested gear ratio is 20:1 but anything between 10:1 and 60:1 is likely to be OK depending on the wheel size used. If you want to use encoders then Pimoroni have extended back shaft 6-volt ones at 11:1, 20:1 and 50:1 gear ratios, all of which would work well. Pololu have similar extended back shaft motors with gear ratios of 5:1, 10:1, 30:1 and 50:1.

### 2.3.4 Motor Voltage

The robot is designed for use with motors rated at 6 volts. Using a battery that delivers between 7.5 and 9 volts means that there is plenty of voltage available for 6-volt motors, with a bit spare to allow for some occasional over voltage power being applied to the motors. Make sure that the motors you use are rated at 6 volts and not 12 volts as some will be.

### 2.3.5 Power Rating

Some vendors offer gearmotors come in different power ratings: Low, Medium, High and High with carbon brushes. The power rating will affect the top speed of the motor (the speed of the robot) and the torque (how fast it can accelerate or control the speed). If you choose a motor that has no stated power rating it will probably be low or medium and will work just fine.

For comparison, a 10:1 6 volt gearmotor from Pololu with no load on it will have the following characteristics:

High Power——————— 3000 RPM 3.0 oz/in torque
High power (carbon brush) – 3000 RPM 2.4 oz/in torque
Medium Power —————– 2200 RPM 1.5 oz/in torque
Low Power ———————- 1300 RPM 1.4 oz/in torque

The High Power motor will require higher current and consume more battery power but is worth using if you want to get maximum performance.

## 2.4 Mechanical parts not in the BOM

Item | Description | Part numbers and supplier options
Wheels and Tyres | Pololu Wheel 32×7mm Pair available in black or white. Alternatively, you can 3D print some 32mm diameter wheels for a 3mm D shaft and use O rings for tyres. | Pi Hut SKU: POL-1087 or SKU: POL-1088<br><br>https://thepihut.com/products/pololu-wheel-32x7mm-pair-black
Motor Mounts | You need 2 motor mounts. They can be 3D printed if you have the capability or you can buy the Pololu motor mounts. 3D print models can be found in the \mechanical folder. GeminiN20MotorMount.STL | Pi Hut code SKU: POL-989 https://thepihut.com/products/pololu-micro-metal-gearmotor-bracket-pair-black
Encoders and encoder cables | Pimoroni JST connected encoders in sideways orientation. These encoders come in 2 orientations and the correct version is included int the link in the next column. You will also need two 6 pin 1mm pitch JST-SH cables to connect the motor encoder to the main board. An adaptor is used to convert the JST-SH cable to 2.54 pitch to connect it to J1 and J2. | https://thepihut.com/products/micro-metal-motor-encoder-mmme-pack-of-2? https://thepihut.com/products/jst-gh-1-25mm-pitch-6-pin-cable-100mm-long https://amzn.eu/d/hsau12j
Encoder adapter board | This board converts JST-SH to 2.54 pins. This does make soldering of the robot easier. You can omit this part if you are comfortable soldering wires from a JST-SH cable direct to the chassis board. Soldering directly to the chassis board is for experienced builders only as it increases the risk of problems connecting the motors and encoders. | https://thepihut.com/products/breakout-for-6-pin-jst-sh-style-connector-side-entry
Battery and connector | The battery should be a PP3 9Volt block. Lithium Ion rechargeables with micro-USB charging socket are ideal. Prefer 1200mAH capacity or greater | https://amzn.eu/d/i8hoP5S https://amzn.eu/d/cmckSHt Rapid Online Order Code: 18-0092

Nuts and bolts | If you are using the Pololu motor mounts you will need 2 M2 x 30mm bolts and nuts for the rear support of the mezzanine board. If you are using 3D printed mounts with 3mm holes, you need 2 M3 30mm bolts, 2 M3 20mm bolts and 4 M3 nuts. Ebay is a good place to order small quantities of M2 and M3 hardware | Rapid Online Order Code: 51-3852 Rapid-Online Order Code: 51-3437 https://www.ebay.co.uk/str/kaysfasteners
Stackable Headers | Used to make the connections between the chassis board and the mezzanine board, 2 connectors 1x6 at 2.54” pitch are required. Stackable headers for many devices are available and can be cut down to provide the 2 connectors required. | https://thepihut.com/products/stacking-header-set-for-raspberry-pi-pico
Stand Offs | Used for mounting the sensor and mezzanine boards. Lots of ways to do this but a pack of standoff's makes this simple. A nylon screw and nut can be used as a skid. | https://amzn.eu/d/eMlVNY3
Screen | Not part of the core build and not essential, but adding a small 1” OLED screen to your robot can be helpful. Choosing the right component the screen can be plugged directly into J5 of the mezzanine board. The important thing with a screen is the pin order which needs to be Gnd, Vcc, SCL, SDA left to right as seen from the top. Other screens can be used but will require custom connectors. *Warning* The screens available from Pimoroni can be used but their GND and Vcc pins are reversed when compared to the mezzanine board connector. EXTREME care needs to be taken if wiring these. | https://www.amazon.co.uk/Fasizi-Serial-Display-Headers-Arduino/dp/B09Z27KV42

# 3 Main Chassis – Buggy

This is the main chassis top of the Gemini V2.1 board

and this is the bottom of the Gemini V2.1 board:

Do not worry if some of the photos in this guide show different colour PCBs, the instructions are the same for your version 2.1 boards.

## 3.1 DRV8833 Motor Controller Board

We will start with the DRV8833 motor controller board. If your DRV8833 board has not got headers soldered in already, put the headers into a breadboard to hold them upright Then put the board on top of them to enable you to solder the headers to the board. Yor 6 pin headers have a short and long lead. Put the long lead into the breadboard and solder the short leads onto the DRV8833 board.

Now you can solder the DRV8833 board onto the main chassis board. Ensure that you put the board in the right way round as shown below with the large yellow capacitor on the left side. Then solder the 2 sets of 6 pins on the bottom of the board.

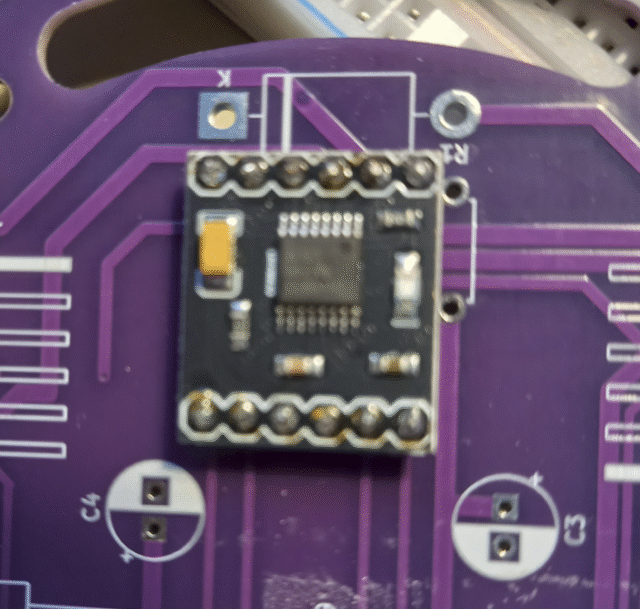
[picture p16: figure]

Next we will add the 47K ohm sleep wake resistor R1 and the polarity protection diode which are next to the DRV8833 board. The 47K ohm resistor (marked yellow purple orange) does not matter which way round it goes, but the protection diode MUST have the silver band on it next to the hole marked K (for cathode). Depending which diode you use it may be larger than the one shown. Solder in both of these components on the bottom of the board.

Next, we will add the two 100uF electrolytic capacitors C3 and C4. Note that both of these are polarised and MUST go in the right way round. The lead on the grey side of the capacitor with the minus sign on it goes in the hole shown white on the printing on the board. Note that the left one of these has the negative side pointing forward and the other has the negative side pointing backwards as shown here. You capacitors may be smaller than these shown depending on the voltage rating and source. Solder both of them on the bottom of the board.

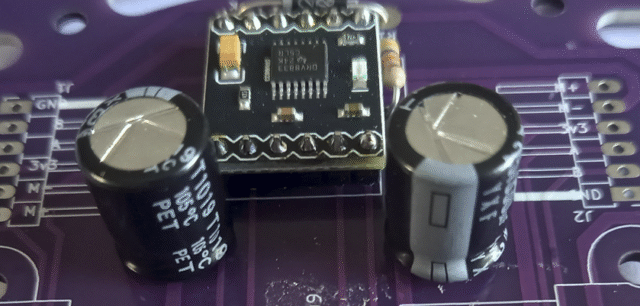
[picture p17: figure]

## 3.2 5 Volt Regulator

Next we will add the 5Volt regulator U2. Put it in so that the flat side is on the outer edge of the board and the black section is towards the labels for 5V, GND and Vbatt. Solder it on the bottom of the board.

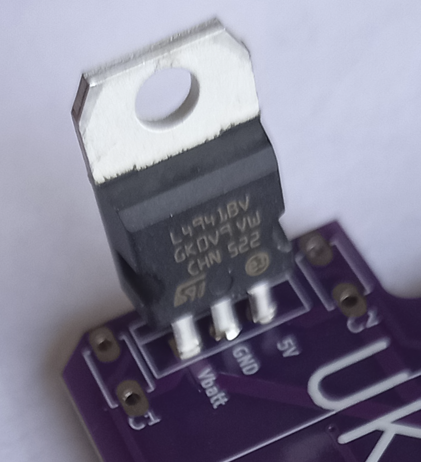
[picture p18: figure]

Using the LM7805 you will have a 0.22uF capacitor for C1 and a 0.1uF capacitor for C2. These can be inserted either way round.

(If you choose to use an alternative regulator eg the L4941BV the capacitors will have different values and you may need to use a polarised capacitor for C2).

## 3.3 Sockets to Connect the Mezzanine Board J3 & J4

Next add the two 6 pin sockets that will connect to the Mezzanine board. If you have a longer strip of sockets, cut them at the 7th socket, which will leave 6 clean sockets to put on the board. Solder one end in first then check that they are fully seated squarely on the board before soldering in the other 5 pins. Repeat for both 6 pin sockets.

## 3.4 On/Off Switch and Battery Connector

Next we will add the on/off switch and battery connector. The on/off switch may just have 3 pins as this one shown or it may also have 2 extra pins used to give extra support to the switch at each end. If you only have 3 pins on your switch, solder it into the middle 3 holes leaving a mounting pad hole at each end. Then add the 2 pin battery connector. Several different 2 pin styles can be used. A simple unpolarised 2 pin connector is shown here.

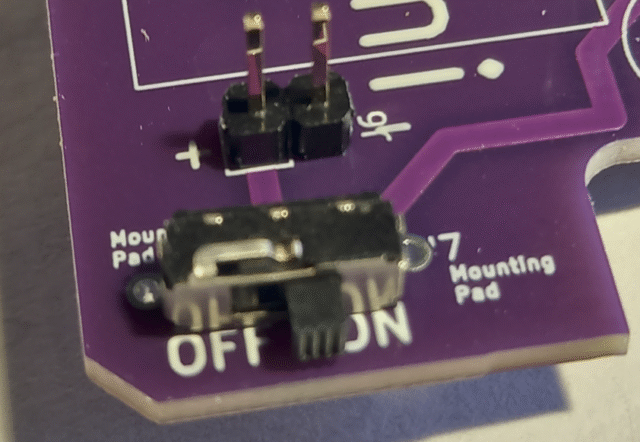
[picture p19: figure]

## 3.5 Connectors for Motors and Encoders J1 & J2

Next we add the motor and encoder connectors J1 and J2 These are two 6 pin JST breakout boards that connect the 2 motor power leads and the 4 encoder leads. The photo shows an early prototype board but the assembly process is the same for the version 2.1 boards.

To solder the 6 pin header to the breakout boards use the same technique described for DRV8833 Motor Controller Board Put the header into a breadboard to hold it upright Then put the board on top of the header to enable you to solder the headers to the board. The header is on one side of the breakout board so you will need to support the other side with a matchstick or similar to keep the board level. Your 6 pin headers have a short and long lead. Put the long lead into the breadboard and solder the short leads onto the breakout board.

Now you can solder the breakout boards onto the main chassis board. Then solder the 2 sets of 6 pins on the bottom of the boards.

Your main chassis board is now ready to add the motors.

If you are not installing encoders, you only need to connect the 2 motor power leads marked M+ and M- You could connect the motor power leads directly to these pads either using right angled header or soldering directly to the board. Take care if you are soldering directly that the joint is sound, complete and has not created any short circuits with nearby components or pads.

# 4 Fitting Encoders and Mounting Motors

## 4.1 Fitting Encoders

GEMINI is designed to use Pimoroni JST connected magnetic encoders in sideways orientation. These only require the encoder shims to be soldered to the motor terminals and the magnets pressing onto the end of the extended shaft so that they are just clear of the components on the encoder shim. Connection from the motor and encoder to the chassis board is achieved through a short JST cable.

Note that the face of the circular magnets that has dimples must face away from the motor. If you install this upside down, the encoder will not work.

Other encoders from Pololu are available that require 6 wires to be soldered to the encoder and have smaller pads to connect to the motor. These are much fiddlier to install and are not recommended. Pimoroni sometimes offer 50:1 motors with the encoder pre-fitted. This can save you a step if you think a 50:1 motor will be quick enough for you. More motors are being offered with encoders pre-fitted – only use these if you are confident that the pin-out is the same as Pimoroni and that they will physically fit on the robot!

## 4.2 Mounting Motors

Now that you have fitted your encoders and attached a short JST cable you are ready to mount you motor/encoder assembly onto the chassis board.

The example here uses standard Pololu motor mounts and substitutes M2 30mm bolts for the rear mounting holes. These long bolts will securely attach the Mezzanine board when it is ready to be assembled.

Organise the nuts, bolts, washers and motor mount then place the motor mount over the gearbox of your motor.

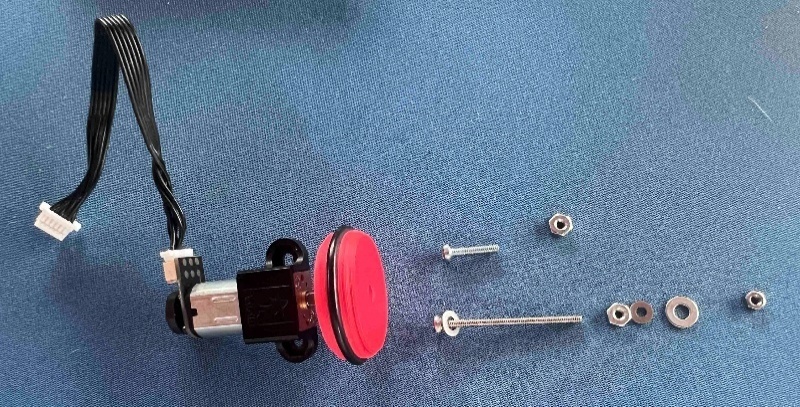
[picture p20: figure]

Start with the front mounting hole and the short bolt. Slip the nut into the motor mount (fiddly) then screw the bolt through from the bottom of the board securing the motor to the board. Do not completely tighten at this stage as you will need to ensure the motor is properly aligned when the second bolt is installed.

Next slip the original nut that came with the Pololu motor mount into the motor mount and feed the long bolt through from the bottom of the board and secure the motor to the board. Before tightening both bolts make sure the motor is properly aligned. The long bolt will now act as a stud to secure the Mezzanine board. You may need a washer between the bolt head and the board depending on the style of bolt you are using.

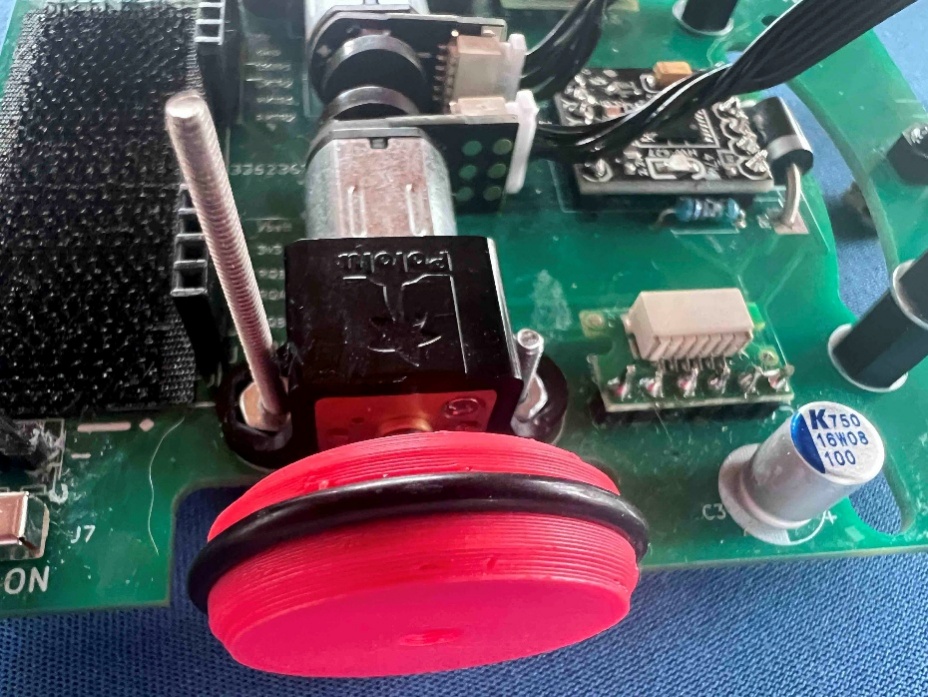
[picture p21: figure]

Loosely fit the nuts and washer to the rear studs that will be used to fix the Mezzanine board so that they are to hand for assembly.

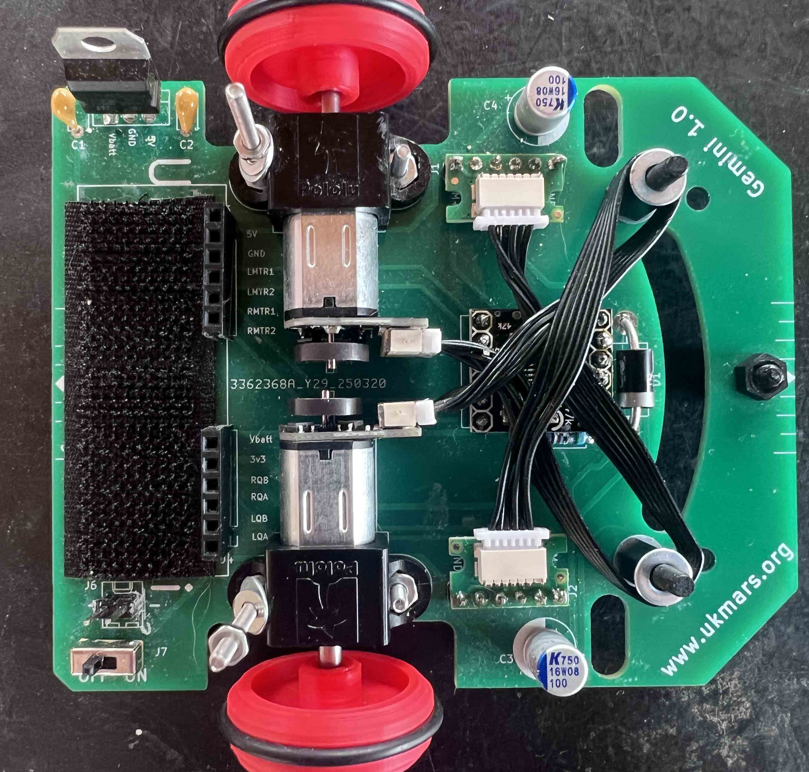
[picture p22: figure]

Finally, you can connect the JST cables into the sockets on the chassis board. Excess cable can be tidied up by taking the cables around the sensor board stand-offs.

Note: When removing the wheels from the shafts DO NOT just try to pull them off as you may damage the gearbox on the motor. If you are using Pololu wheels use a small screwdriver to expand the slit in the wheel hub to open up the D shape loosening its grip and slide the wheel off the shaft.

If you are using 3D printed wheel with no expansion slit use a small screwdriver inserted between the gearbox and the wheel hub, and lever the wheel off the shaft this way.

If you are using 3D printed motor mounts based on https://github.com/ukmars/gemini/blob/main/mechanical/GeminiN20MotorMount.stl

then you will need two M3 30mm bolts, two shorter M3 bolts, four M3 nuts and some M3 washers. If you are able to print these mounts they are less fiddly than the Pololu mounts and the M3 bolts are easier to work with than the M2 bolts on the Pololu mounts.

You are now ready to decide which sensor board you want to build to fit to this GEMINI robot. You only need to build one, either

- the Line Sensor Board for line following, drag racing and the pursuit challenge or
- the Wall Sensor Board for wall following and maze solving.

You may choose to build both sensor boards so that your GEMINI robot can be re-purposed to either sets of challenges but you can always come back later to build your second choice of sensor board. If you are new to robot building, the line events offer a gentler learning curve to acquiring the necessary skills.

# 5 Line Sensor Board

This is a view of the top of the PCB

This is the bottom of the PCB

## 5.1 The Resistors

We start by adding the resistors. There are 15 of these of 6 different values so be careful which ones go where. Bend the leads over as close to the body of the resistors to get them to fit into the holes. The descriptions in the text give the colour coding for 3 band resistors. You can identify the correct value resistors (3,4 or 5 band) using Appendix B – Resistor Colour Code Chart

Check the value of your resistors with your multi-meter before you solder them in.

R7, R8, R9 and R14 are all 680 ohms (colour banded green, grey, brown) so put these in first. (The resistors shown in these photographs are for a pre-production board and are not 680 ohms so yours will have a different colour coding -check they are 680 ohms before soldering,)

Then add R3, R5 and R17 which are all 10 ohms (colour banded brown, black, black) shown here with blue bodies.

Then add R10, R11 and R12 which are all 680 ohms (colour banded green, grey, brown)

Then add R4 and R16 which are 10K ohms (colour banded brown, black, orange)

Then add R2 and R15 which are 390 ohms (colour banded orange, white, brown) Do not get these mixed up with 39 ohm resistors which have just the final band different.

Then finally add R1 which is 47 ohms or 33 ohms (colour banded orange, orange, black). Either value is ok.

You should now have all 15 resistors in place. Check them before going further with the build.

## 5.2 The Transistors

New we will add the two BC337-40 transistors Q1 and Q6. Insert them so that the flat side matches the flat side shown on the screen print. Q1 has the flat side at the back, while Q6 has the flat side at the front.

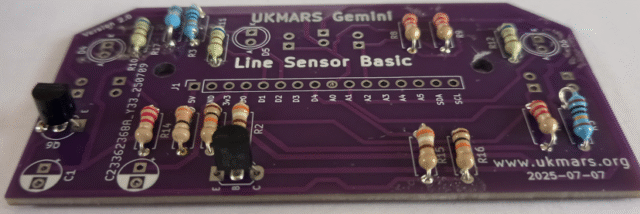
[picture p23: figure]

## 5.3 The Indicator LEDs

Now put in the 3 indicator LEDs D4, D5 and D6 put the longer lead at the hole marked A (for Anode) It is suggested that you use one red, one yellow and one green one to make it easiest to tell which is lit when it is moving. These are the low current LEDs just used as indicators. Do not put the high brightness RED LEDs in these positions

## 5.4 The Capacitors

Next to go on the top of the board are the electrolytic capacitors C1 and C2. Ensure that they go in with the negative strip on the side of the capacitors at the back of the board where the white segment is shown on the screen print.

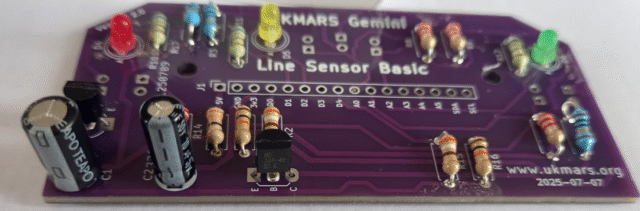
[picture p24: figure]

## 5.5 The Mezzanine Connector J1

The last item to go on the top of the board is the 16-way female socket which will make the connection to the mezzanine board for all the circuits. Solder this in carefully on the bottom of the board, making sure that it is seated fully down on the board and upright.

## 5.6 Devices on the Underside of the Board

The other parts go on the underside of the board and are soldered on the top. These devices will look down through the apertures in the chassis board to sense the line geometry. The LEDs are the larger 5mm parts and the phototransistors the smaller 3mm parts.

### 5.6.1 Illumination LEDs

First put in the 3 illumination LEDs One goes in the centre and one on each side. Make sure that the long lead goes on the hole marked A (for Anode). Note that on one side the Anode is towards the front and on the other side it is towards the back. The base of the LEDs need to stand proud of the board by about 5mm. To get this correct amount, spread the leads slightly before you put them in the holes then put them in until the slight notch on the leads touches the board. Now solder one lead then check both the distance from the board and that the LED is standing precisely upright. If needed, adjust the height or angle then solder the other lead.

### 5.6.2 Phototransistors

Now put in the 4 BPW85C phototransistors Q2, Q3, Q4 and Q5. Make sure that the long lead goes in the hole marked E (for Emitter). Set them at the same height off the board as the LEDs and use the same process as above to get the height and angle correct. Note that the emitter is towards the back of the board for Q5 while for all the other three the emitter is towards the front

Your line sensor board is now complete

# 6 Wall Sensor Board

This is the view of the top of the PCB

This the bottom of the PCB

## 6.1 The Resistors

We start by adding the resistors. There are 14 of these of 7 different values so be careful which ones go where. Bend the leads over as close to the body of the resistors to get them to fit into the holes.

The descriptions in the text give the colour coding for 3 band resistors. You can identify the correct value resistors (3,4 or 5 band) using Appendix B – Resistor Colour Code Chart

Check the value of your resistors with your multi-meter before you solder them in.

First add the resistor R2, 33 ohms (colour banded orange, orange, black) which is used for power decoupling and then R7, R8 and R9 resistors of 10 ohms (colour banded Brown, black, black) which are the three wall illumination LED load resistors

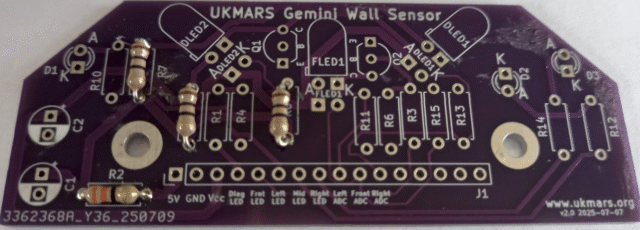
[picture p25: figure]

Next add R1 and R3 both 390 ohms (colour coded orange, white brown) used to current limit the current to the bases of the two transistors which switch the LEDs off and on

Then add R4 and R6 both 10K ohms (colour banded brown, black, orange) which provide the bias for the base of the transistors

Now add the 3 phototransistor load resistors. R11 and R13 are 2.2K ohms (colour coded red, red, red) but R15 is 1.8k ohms (colour coded brown, green, red). This is to give the front sensor more range.

Finally go in the 3 indicator LED load resistors R10, R12 and R14, all at 680 ohms (colour coded green, grey, brown)

## 6.2 The Indicator LEDs

Next add the 3 low current indicator LEDs D1, D2 and D3. Make sure that the long lead goes into the hole marked A (for Anode) Note that not all of the LEDs are oriented in the same direction. Use 3 different colours for them e.g. red, yellow and green as shown here:

## 6.3 The Transistors

Now we will add the 2 transistors Q1 and Q2 marked BC337-40 Make sure that they go in with the flat side as shown towards the text FLED1 matching the layout shown on the board

## 6.4 The Mezzanine Connector J1

Now we can add the 16-way female socket that connects to the mezzanine board. Solder in a pin at each end then check that it is seated fully down on the PCB and upright before soldering in the rest of the pins

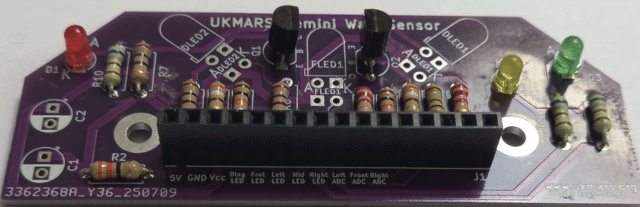
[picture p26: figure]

Now we just have the wall illumination LEDs and phototransistors to go in.

## 6.5 The Illumination LEDs

The three LEDs sit on the top of the board and are soldered beneath, but the phototransistors sit below the board and are soldered on the top. You must put the LEDs in first using the holes closest to the outline of the LED with the long lead going in the hole marked A (for Anode), as shown here.

Bend the LEDs like this, making sure that the long lead is on the left ready to go in the A hole. Do not mount these too tightly to the board because you will need to adjust their posture later.

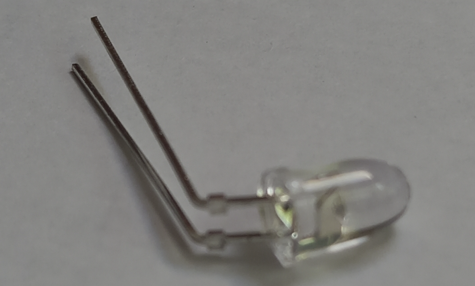
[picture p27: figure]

Once they are soldered they should look like this

## 6.6 The Phototransistors

Now turn the board over and add the 3 BPW85C phototransistors RDPD1, FPD1 and LDPD1 putting the long lead in the hole marked E (for Emitter). Solder them on the top of the board just behind where the LED leads go through. The phototransistors should point in the same direction as the LEDs, one forward and two angled at about 45 degrees towards the side. Put a piece of paper beneath the leads while you solder them so that they do not short on the LED contacts below as shown.

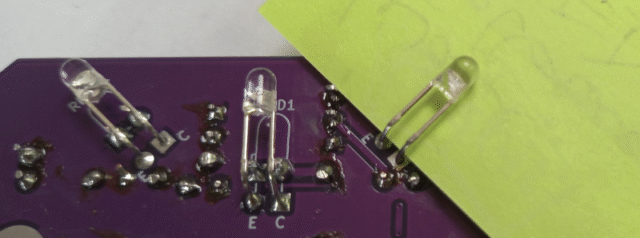
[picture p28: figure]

## 6.7 The Capacitors

Then we will add the 2 100uF 16V electrolytic smoothing capacitors. They should be the 7mm high versions as specified in the parts list. They are polarised so make sure that the minus sign on the side goes to the back of the board on the white section of printing.

Your wall sensor board is now complete

# 7 Mezzanine Processor Board

This is the top of the Gemini V2 Mezzanine board for the Raspberry Pi Pico RP2040 processor.

And this is the bottom of the Mezzanine board for the Raspberry Pi Pico RP2040 processor.

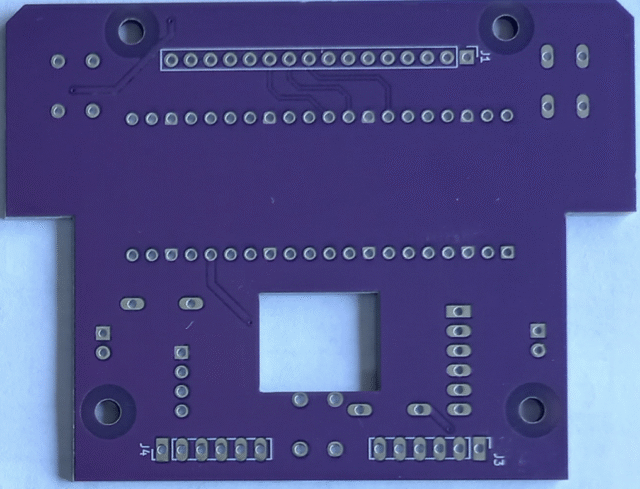
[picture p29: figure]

There are only a few components to be added other than connectors.

## 7.1 The Switches

We will start by adding the 3 tactile switches SW1, SW2 and SW3 the RESET button. They will only go in one way round so carefully align the pins on then and push then through so as to fit flush on the board, then solder them in. Here are the positions of tactile switches SW1 and SW2 at the front of the board.

This is followed by tactile switch SW3 on the back of the board next to the word RESET

## 7.2 The Resistors

Next are R1 and R2, the 680 ohm (coded green, grey, brown) LED load resistors.

## 7.3 The Indicator LEDs

Note also the position of LEDs D1 and D2 which are marked K(for cathode) and A (for Anode) in the image above. The long lead goes in the side marked A and the short lead goes in the side marked K. Two different colour LEDs are recommenced as shown below. Do not use blue or white ones as they require higher voltages so may not work.

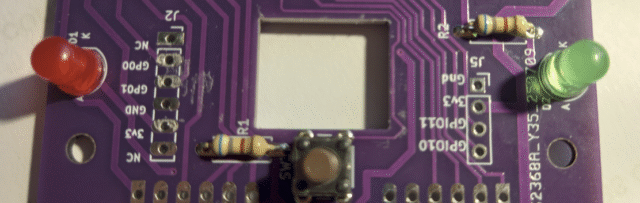
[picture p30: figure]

## 7.4 Connectors and Sockets

Now we are ready to add headers and sockets. The sensor board connector at the front of the board uses a 16-pin header. It is put in on the underside of the board and hence soldered on the top surface as shown.

Then add the two breakout sockets J2 and J5. J2 is a 6 pin socket and J5 is a 4 pin socket. Solder them on the bottom of the board next to the LEDs as shown.

Now add the two 6 pin connectors which go below the board and are soldered on the top of the board. They are either side of the RESET tactile switch.

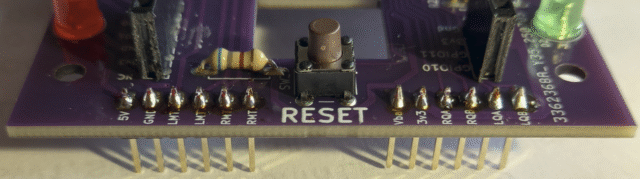
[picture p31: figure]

If your Pico Processor board is to be socketed, add the two 20 pin sockets for that,

Putting the Pico into the socket means that it will now look like this: Make sure that it is put in so that the USB micro socket matches the square shown on the screen print and next to tactile switch SW1

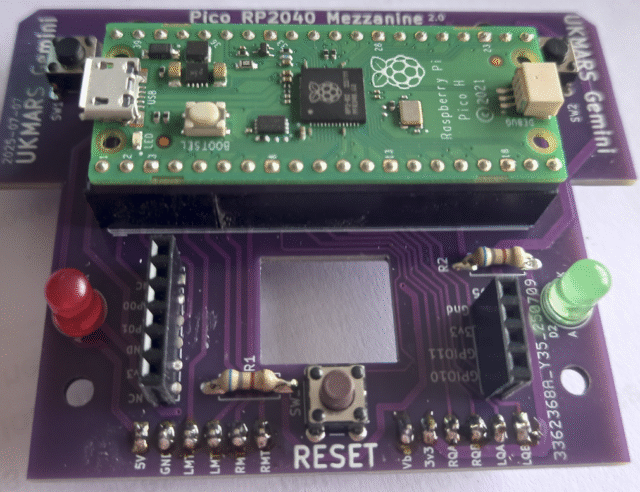
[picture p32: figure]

Your mezzanine processor board is now complete.

# 8 Putting It All Together

Now you have assembled all the PCBs it’s time to build the complete GEMINI robot.

## 8.1 Skids

The GEMINI robot only has 2 wheels like a chariot so it needs skids front and rear to keep it level. The robot needs to be able to rock up and down at the front and rear so that under acceleration the wheels are in contact and the robot is rocked back onto the rear skid for stability. Under braking the front skid stabilises the robot.

If you do not allow enough up and down movement between acceleration and braking your robot will get “beached” when both skids are in contact with the running surface and the wheels will not make sufficient contact to gain traction. Too much freedom to rock up and down and your sensors will become ineffective either shining down into the surface or up into the sky.

It is worth spending some time to get this setup correctly. The free up and down movement at the front of the robot should be about 3mm (the difference between the lowest point and the highest point constrained by the skids with the wheels on the ground).

### 8.1.1 Materials to Make Skids

Skids can readily be made from plastic stand-off parts using the head cut from a metal paper fastener as shown. Height adjustment is achieved by filing down the plastic parts until the desired heights are reached and glueing the fastener head over the plastic stud. Remember to allow for the fastener head to adjust the heights before glueing!

## 8.2 Front Skid

It is easy to attach the front skid to the dedicated hole in the PCB, simply insert the threaded end of the skid and secure with a nut.

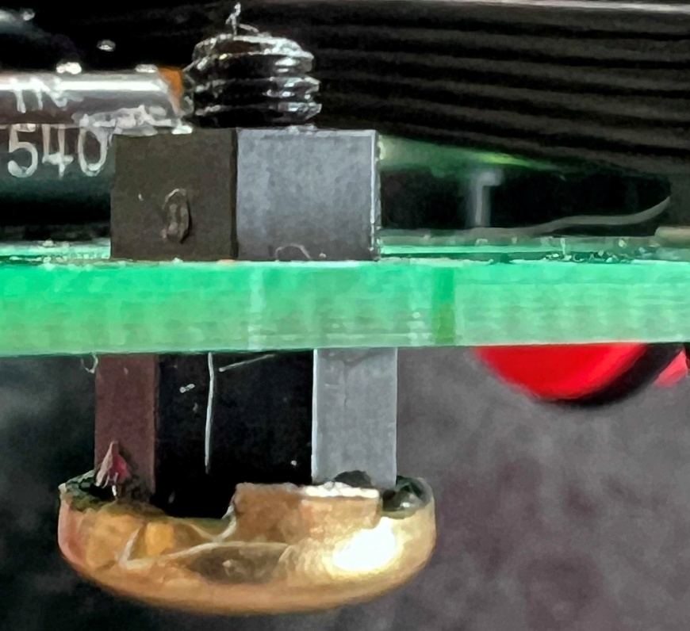
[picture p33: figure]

### 8.2.1 Rear Skid

It is better to glue the rear skid into the dedicated hole on the chassis board and make sure that none of the threaded end of you skid protrudes above the top of the chassis board. This leaves the space reserved for the battery flat and it will sit much better. Velcro is a good way to secure your battery.

## 8.3 Attach the Sensor Board to the Chassis

The sensor board is attached to the chassis boar using M3x8+6mm stand-offs. This means the diameter of the thread is 3mm the body of the stand-off is 8mm and the threaded stud is a further 6mm long.

The stand-off is attached to the chassis board by inserting M3x6mm bolts through the holes in the chassis board and screwing the stand-offs down onto these.

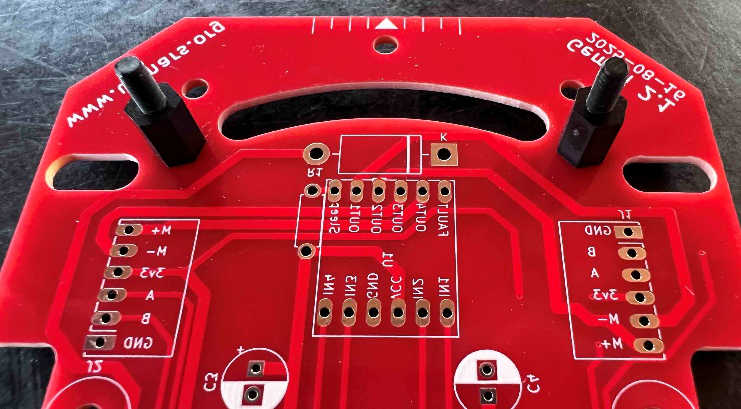
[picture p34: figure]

The sensor board is placed over the protruding studs of these stand-offs and secured in place by screwing down 2 M3x10+6mm stand-offs

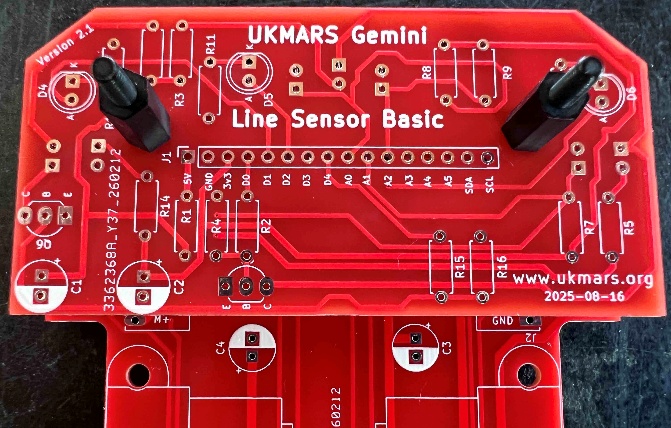
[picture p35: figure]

## 8.4 Attach the Mezzanine Processor Board

The connections between the chassis and mezzanine boards are achieved using extended headers inserted into J4 and J5 on the chassis board.

First prepare two 6pin extended header sockets by cutting down a strip of extended header. Shorten the conductor pins of the header so that they can fully insert into the standard headers for J4 and J5 and sit snuggly on top of the standard header socket.

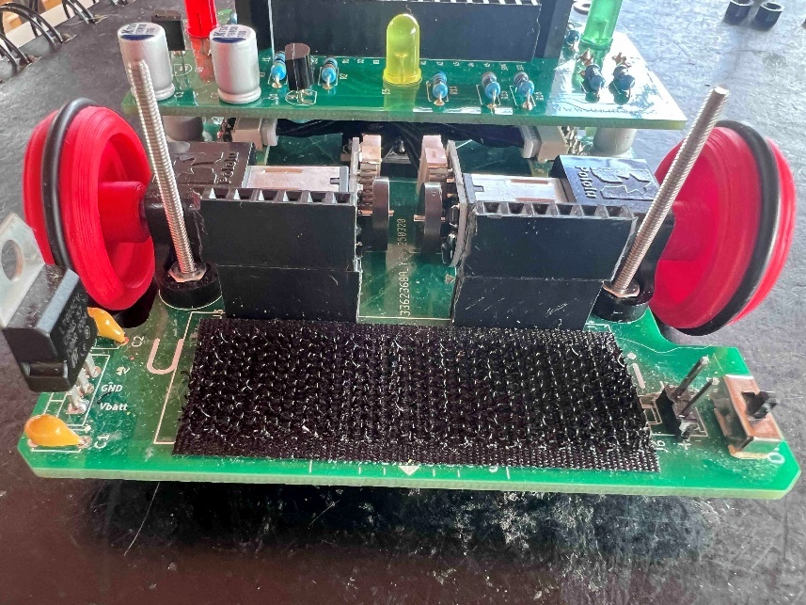
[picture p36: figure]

Now carefully place your mezzanine board onto the chassis and sensor boards aligning the mounting studs from these boards through the holes in the mezzanine board. Do not press the mezzanine board down.

Check to make sure that all the connecting pins are properly aligned with their receiving sockets.

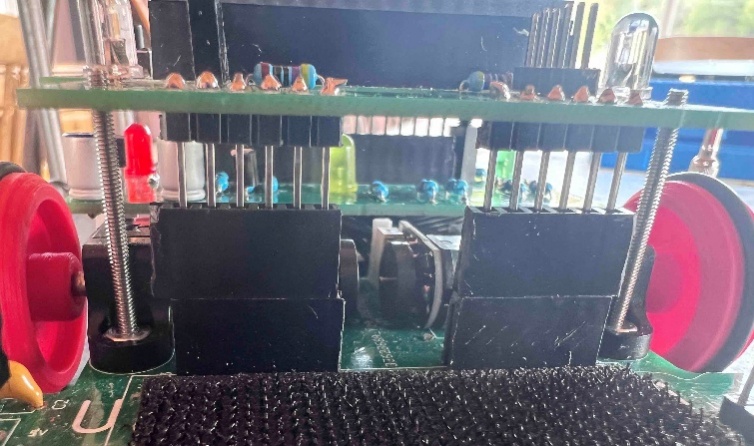
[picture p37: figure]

When you are sure that everything is lined up properly, gently and evenly press the mezzanine board down into the sockets on the chassis and sensor boards.

Now secure the boards with the nuts and washers. Do not overtighten these nuts or you will start to bend the PCBs.

The mezzanine board will be at a very slight angle to the chassis board and this is perfectly fine, note the sensor board is parallel to the chassis board and this is important for reliable sensor readings.

If you are offended by the slight angle of the mezzanine board you can cut the extended header pins to a longer length leaving exposed pins between the headers.

This method is not recommended as it is mechanically weaker and leaves exposed conductors between the 2 boards that could be shorted accidentally.

## 8.5 Connect the Battery – Your GEMINI robot is complete!

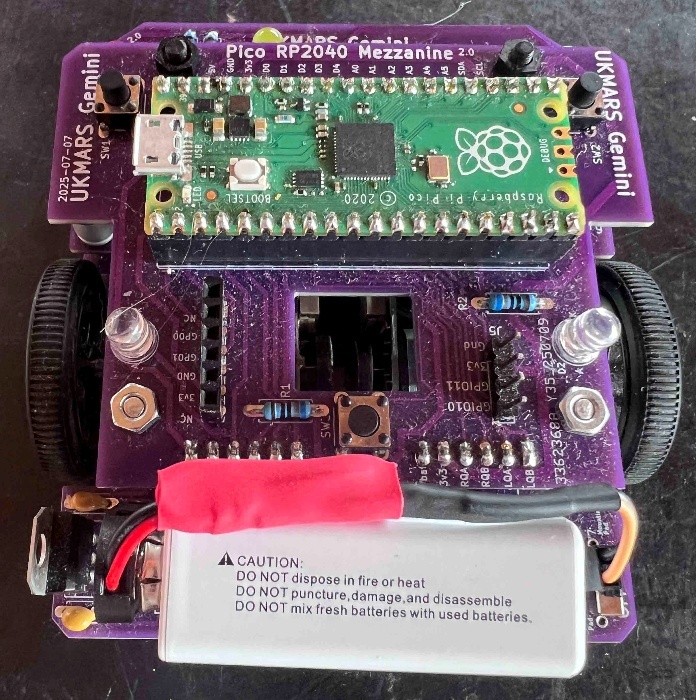
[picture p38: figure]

# 9 Testing, Coding and Further Reading

The easiest and best way to access all the designs, support documents and code examples is to visit out GitHub repo at https://github.com/ukmars/gemini/

See How to access reference and support documents

## 9.1 Test your GEMINI Hardware

Check that everything is working as it should be. If you are building with the line follower sensor board there is diagnostic software published on the GitHub repository:

https://github.com/ukmars/gemini/blob/main/sampleCode/lineFollowerDiagnostics/GeminiLFdiagnostics.py

If you are building with the maze sensor board, modify the line follower board diagnostics to reflect the pin assignments and usages for the different sensor board.

## 9.2 Reference Documents

Documents including schematics and board layouts are published on the GitHub repository:

https://github.com/ukmars/gemini/tree/main/docs

## 9.3 Example Code

An example line follower program to help get started is published on the GitHub repository:

https://github.com/ukmars/gemini/blob/main/sampleCode/GeminiLineFollower.py

An example line follower program to help get started is published on the GitHub repository:

https://github.com/ukmars/gemini/blob/main/sampleCode/DH_WallFollow_example.py

GitHub Repository

Visit our GitHub repository and download a zip copy or clone to your device to have instant access to all the support materials.

https://github.com/ukmars/gemini

# 10 Appendix A – Example Bill Of Materials (BOM)

This BOM was accurate in August 2026 and is included to show the information that is available. Please see https://github.com/ukmars/gemini/blob/main/docs/all_projects_bom.csv for the current BOM.

Project | Reference | Value | Qty | Note | Description | RSONLINE | RAPID
Line Sensor | C1 C2 | 100uF | 2 | | Polarized capacitor | 176-3779 | Nov-09
Line Sensor | D1 D2 D7 | TLCR5800 | 3 | | | 818-7540 | 55-0066
Line Sensor | D4 | Radius | 1 | | | "228-6004 or 228-5562 or 713-3974 or 813-4845" | 56-0400
Line Sensor | D5 | Line | 1 | | | "228-6004 or 228-5562 or 713-3974 or 813-4845" | 56-0405
Line Sensor | D6 | S/Finish | 1 | | | "228-6004 or 228-5562 or 713-3974 or 813-4845" | 56-0410
Line Sensor | J1 | Conn_01x16 | 1 | https://uk.rs-online.com/web/p/pcb-sockets/6816820 Need to be cut down | Generic connector, single row, 01x16, script generated (kicad-library-utils/schlib/autogen/connector/) | 681-6820 | 19-0087
Line Sensor | Q1 Q6 | BC337-40 | 2 | | | 671-1119 | 50-3113
Line Sensor | Q2 Q3 Q4 Q5 | BPW85C | 4 | | | 815-1263
Line Sensor | R1 | 47R | 1 | | Resistor | 707-8817 | 62-0334
Line Sensor | R2 R15 | 390R | 2 | | | 707-7634 | 62-0360
Line Sensor | R3 R5 R17 | 10R | 3 | | | 707-8580 | 62-0326
Line Sensor | R4 R16 | 10K | 2 | | | 707-7745 | 62-0394
Line Sensor | R7 R8 R9 R10 R11 R12 R14 | 680R | 7 | | | 707-8211 | 64-0068
Chassis | BT1 | 9v Battery | 1 | | PP3 9v Battery
Chassis | C1 | 0.22uF | 1 | Maximum height is 10mm | Unpolarized capacitor | 194-0629 | Nov-49
Chassis | C2 | 0.1uF | 1 | Maximum height is 10mm | Unpolarized capacitor | 538-1433 | Nov-42
Chassis | C3 C4 | 100uF, 16V | 2 | Maximum height is 10mm | | 176-3779 176-3779 | Nov-09
Chassis | D1 | 1N5401 | 1 | Polarity protection diode | | 628-9451
Chassis | J1 J2 | Pololu Item #4772 | 2 | 6 pin 0.1" breakout 6 pin header, 0.1", male | Single row, 01x06, JST-SH breakout | | 22-0795
Chassis | J3 J4 J6 J7 | Conn_01x06 | 4 | Might be easier and cheaper to just cut from bigger lengths 0.1" pitch, polarised, any type | https://uk.rs-online.com/web/p/pcb-headers/6812994 | 681-2994 | 01-5723 08-5765 78-0566
Chassis | M1 M2 | N20 MOTOR | 2 | Sidways or regular would work for starting out 50:1 gearbox is recommended commercial mounts need bushing for screws | https://shop.pimoroni.com/products/micro-metal-motor-encoder?variant=39888423321683 | NA
Chassis | R1 | 47K | 1 | | Resistor | 707-8369 | 62-0410
Chassis | U1 | DVR8833_DC_Controller | 1 | | DC Motor Controller https://amzn.eu/d/csv7cRr as an option
Chassis | U2 | LM7805_TO220 | 1 | | Positive 1A 35V Linear Regulator, Fixed Output 5V, TO-220 | 793-1346
Mezzanine | D1 D2 | LED | 2 | | Light emitting diode | "228-6004 or 228-5562 or 713-3974 or 813-4845" | 56-0400 and 56-0405
Mezzanine | J1 J2 J3 J4 J5 | Conn_01x16 | 5 | Might be easier and cheaper to just cut from bigger lengths Cut from a bigger strip of 2.54 header | Generic connector, single row, 01x16, script generated (kicad-library-utils/schlib/autogen/connector/) Generic connector, single row, 01x06, script generated (kicad-library-utils/schlib/autogen/connector/) Generic connector, single row, 01x04, script generated | 681-3007 681-2994 | 08-7948 01-5723 01-5835
Mezzanine | R1 R2 | 680R | 2 | | Resistor | 707-8211 | 64-0068
Mezzanine | SW1 SW2 SW3 | TACT_SW | 3 | | TACT switch 6mm 4.5mm | 479-1390P | 78-3821
Mezzanine | U1 | Pico | 1 | | | | 08-7949 and 75-1230
Wall Sensor | C1 C2 | 100uF, 16v | 2 | | Unpolarized capacitor | 739-6799 | Nov-19
Wall Sensor | D1 D2 D3 | LED | 3 | | Light emitting diode | "228-6004 or 228-5562 or 713-3974 or 813-4845" | 56-0400 or 56-0405 or 56-0410
Wall Sensor | DLED1 DLED2 FLED1 | TLCR5800 | 3 | | Light emitting diode | 818-7540
Wall Sensor | FPD1 LDPD1 RDPD1 | BPW85C | 3 | | Photodiode | 815-1263
Wall Sensor | J1 | Conn_01x16 | 1 | https://uk.rs-online.com/web/p/pcb-sockets/6816820 Can also be found on ebay slightly cheaper | Generic connector, single row, 01x16, script generated (kicad-library-utils/schlib/autogen/connector/) | 681-6820 | 19-0087
Wall Sensor | Q1 Q2 | BC337-40 | 2 | | NPN transistor, emitter/base/collector | 671-1119 | 50-3113
Wall Sensor | R1 R3 | 390R | 2 | | Resistor | 707-7634 | 62-0360
Wall Sensor | R10 R12 R14 | 680R | 3 | | Resistor | 707-8211
Wall Sensor | R11 R13 | 2k2 | 2 | | Resistor | 707-8255 | 62-0378
Wall Sensor | R15 | 1k8 | 1 | | Resistor | 707-8675 | 62-0376
Wall Sensor | R2 | 33R | 1 | | Resistor | 707-8805 | 62-0334
Wall Sensor | R4 R6 | 10K | 2 | | Resistor | 707-7745 | 62-0394
Wall Sensor | R7 R8 R9 | 10R | 3 | | Resistor | 707-8580 | 62-0326

# 11 Appendix B – Resistor Colour Code Chart

GEMINI Build Guide – draft 0.2 02/09/26 Page 1 | 1

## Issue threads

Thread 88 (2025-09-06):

System level schematic

micromouseonline, 2025-09-06:
Is there a system level schematic or other diagram showing how the boards are interconnected and what the pins are?

Or did I just fail to find it?

If there is not, shall I do one?

davidhannaford, 2025-09-06:
Hi peter

Having another go at loading Quadratic

I swapped over the 2 jumpers on the discovery board and it programmed the chip on the discovery board with the quadratic code OK.

I didn’t have STM32Cube Programmer open when I did that

I removed the jumpers on the discovery board and tried to program quadratic again but I failed with :

Error: timed out while waiting for target halted

embedded:startup.tcl:1516: Error: ** Unable to reset target **

in procedure 'program'

in procedure 'program_error' called at file "embedded:startup.tcl", line 1553

at file "embedded:startup.tcl", line 1516

I also tried the loadup with STM32Cube programmer open and connected and it failed with a different error:

Error: libusb_open() failed with LIBUSB_ERROR_ACCESS

Error: open failed

in procedure 'program'

** OpenOCD init failed **

Whatever has happened, now when I read the chip with STM32Cube programmer it is now showing all Hex FFs so the program that was in the chip has now gone.

Should I need to have STM32Cube programmer open and connected when I do the programming ?

Any thoughts or ideas welcomed

Cheers

David

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

IanSuper7, 2025-09-07:
No diagram but a cross reference list in the ecad [folder](https://github.com/ukmars/gemini/blob/main/ecad/GeminiV2PicoPins.pdf)

micromouseonline, 2025-09-07:
I will make a picture.

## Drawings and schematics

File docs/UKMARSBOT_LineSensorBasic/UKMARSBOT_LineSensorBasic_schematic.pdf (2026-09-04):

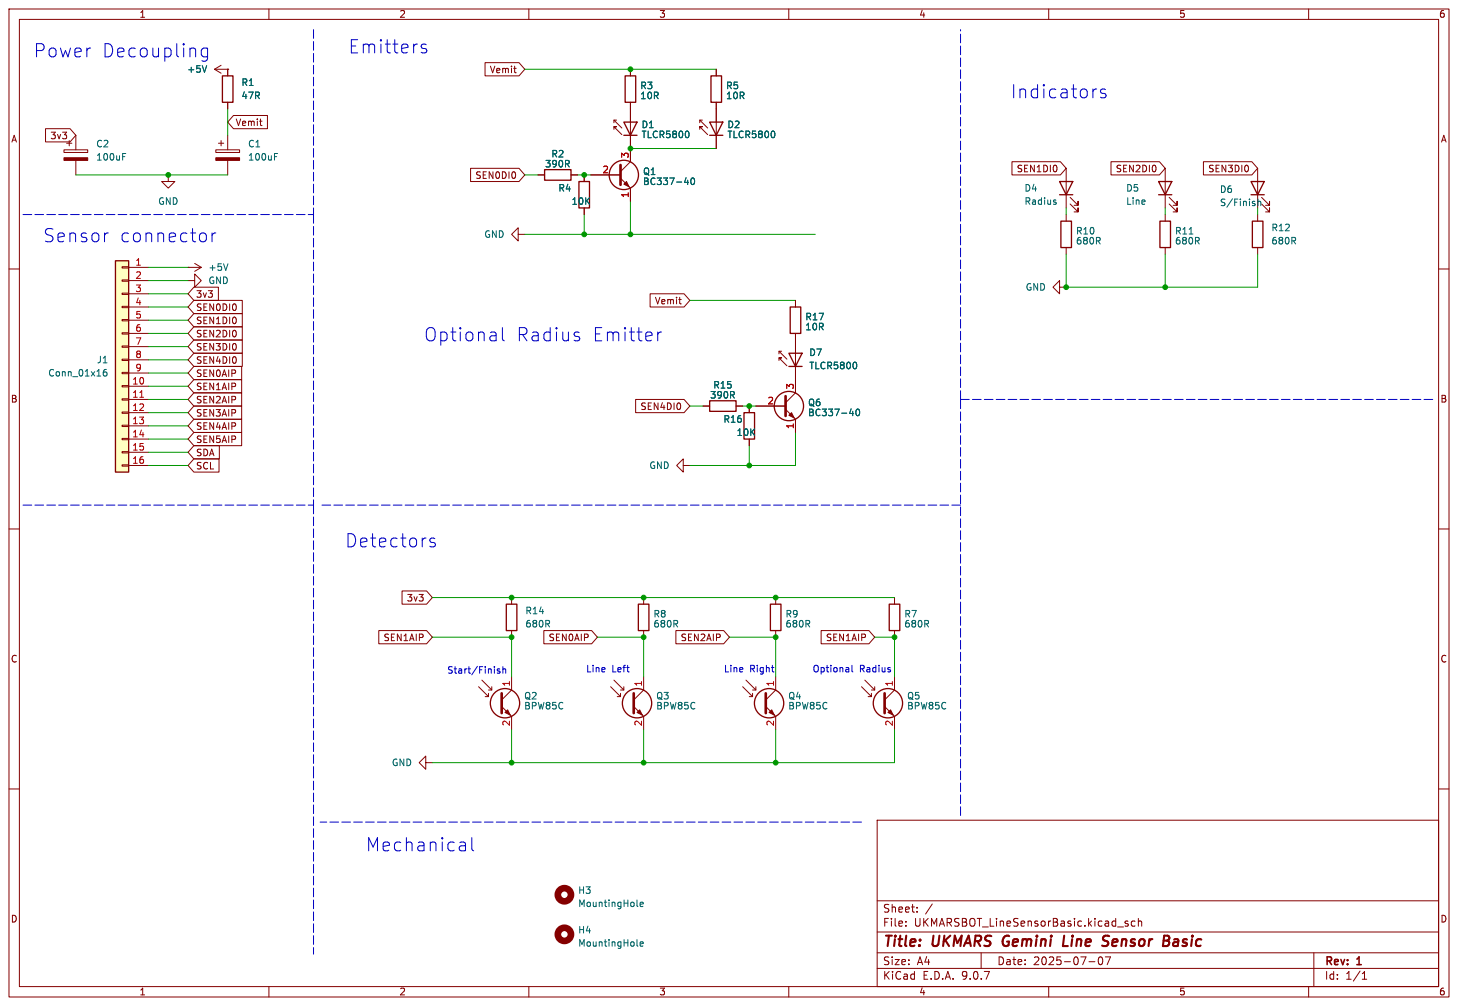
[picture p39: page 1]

File: UKMARSBOT_LineSensorBasic.kicad_sch Sheet: /
Id: 1/1 Title: UKMARS Gemini Line Sensor Basic

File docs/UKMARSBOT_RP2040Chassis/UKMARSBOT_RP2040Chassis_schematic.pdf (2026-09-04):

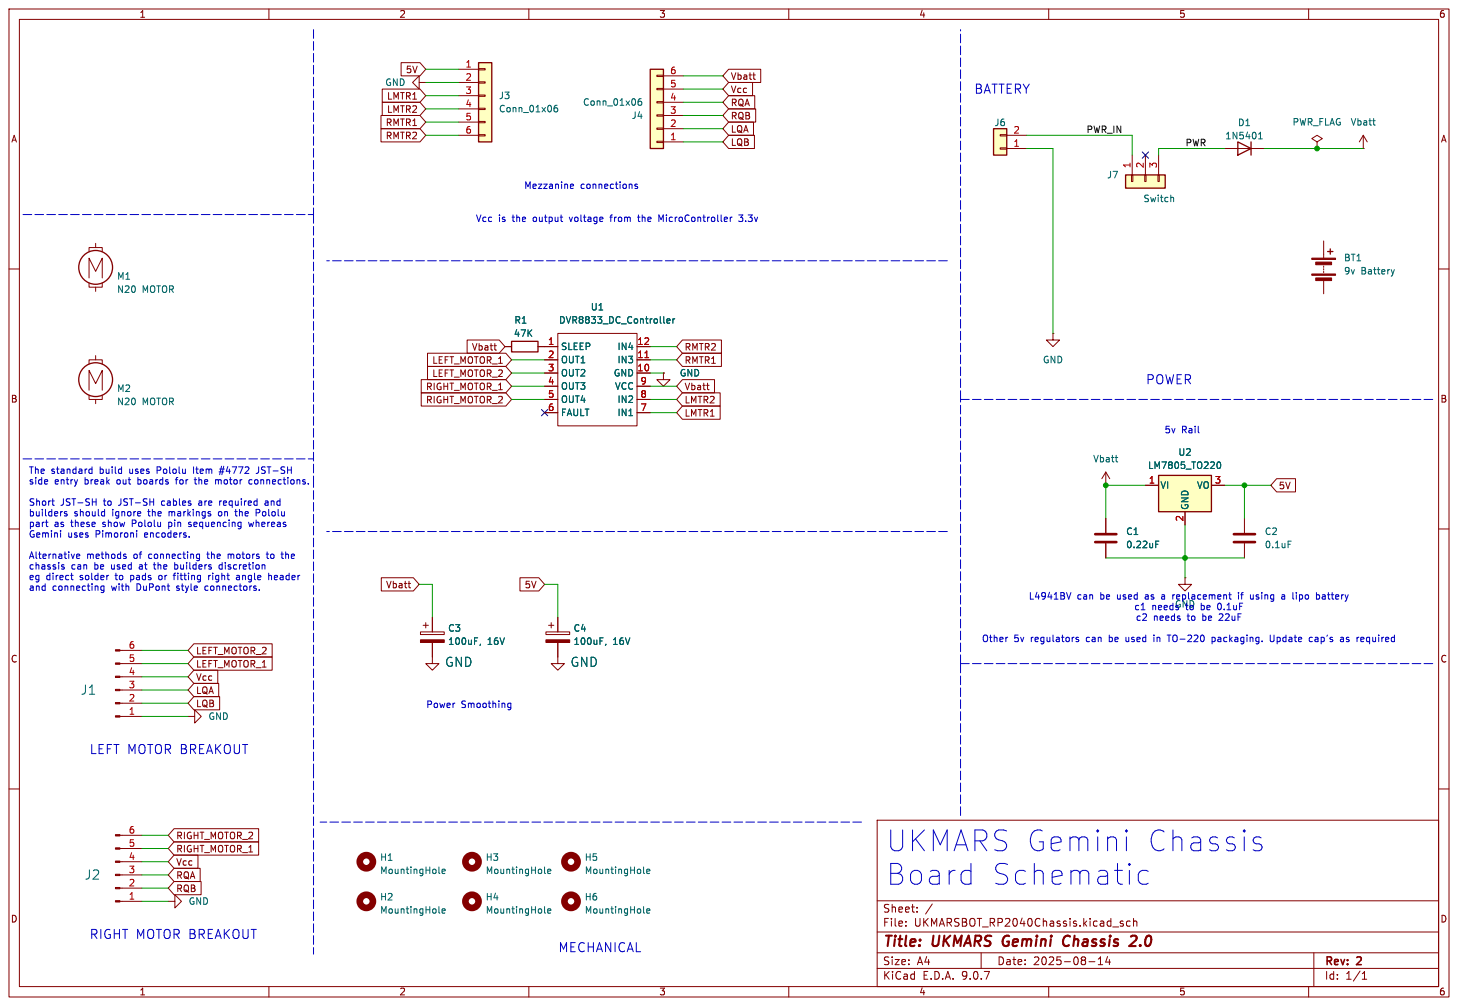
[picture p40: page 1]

Id: 1/1 Title: UKMARS Gemini Chassis 2.0

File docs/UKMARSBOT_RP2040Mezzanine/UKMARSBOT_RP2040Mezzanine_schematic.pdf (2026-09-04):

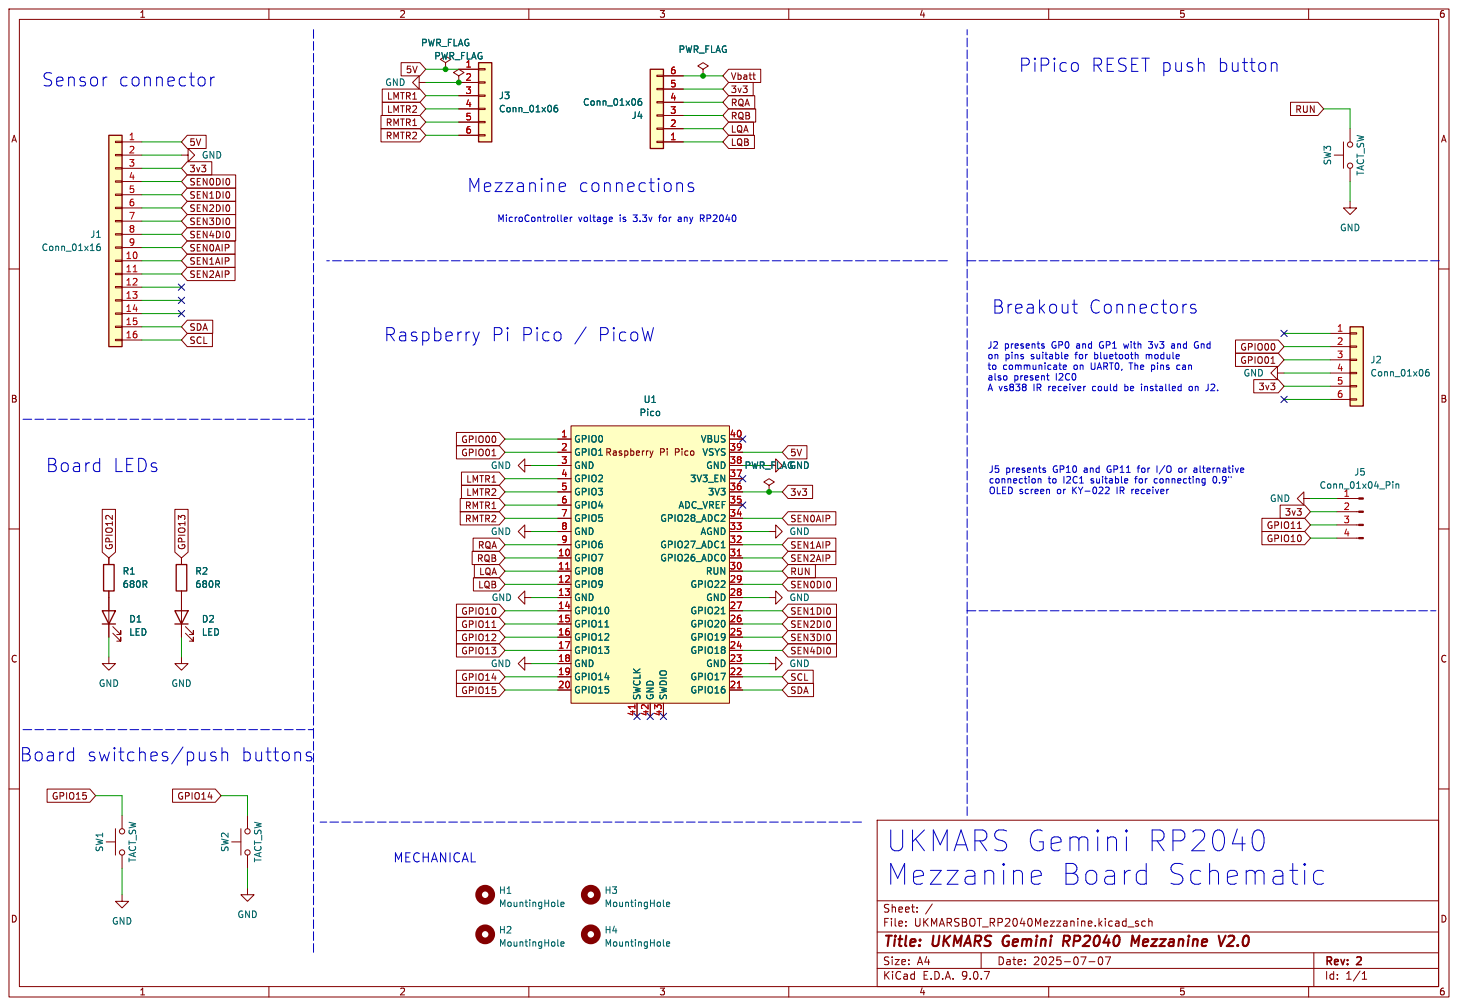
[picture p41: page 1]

Raspberry Pi Pico / PicoW

J2 presents GP0 and GP1 with 3v3 and Gnd

J5 presents GP10 and GP11 for I/O or alternative

Id: 1/1 Title: UKMARS Gemini RP2040 Mezzanine V2.0

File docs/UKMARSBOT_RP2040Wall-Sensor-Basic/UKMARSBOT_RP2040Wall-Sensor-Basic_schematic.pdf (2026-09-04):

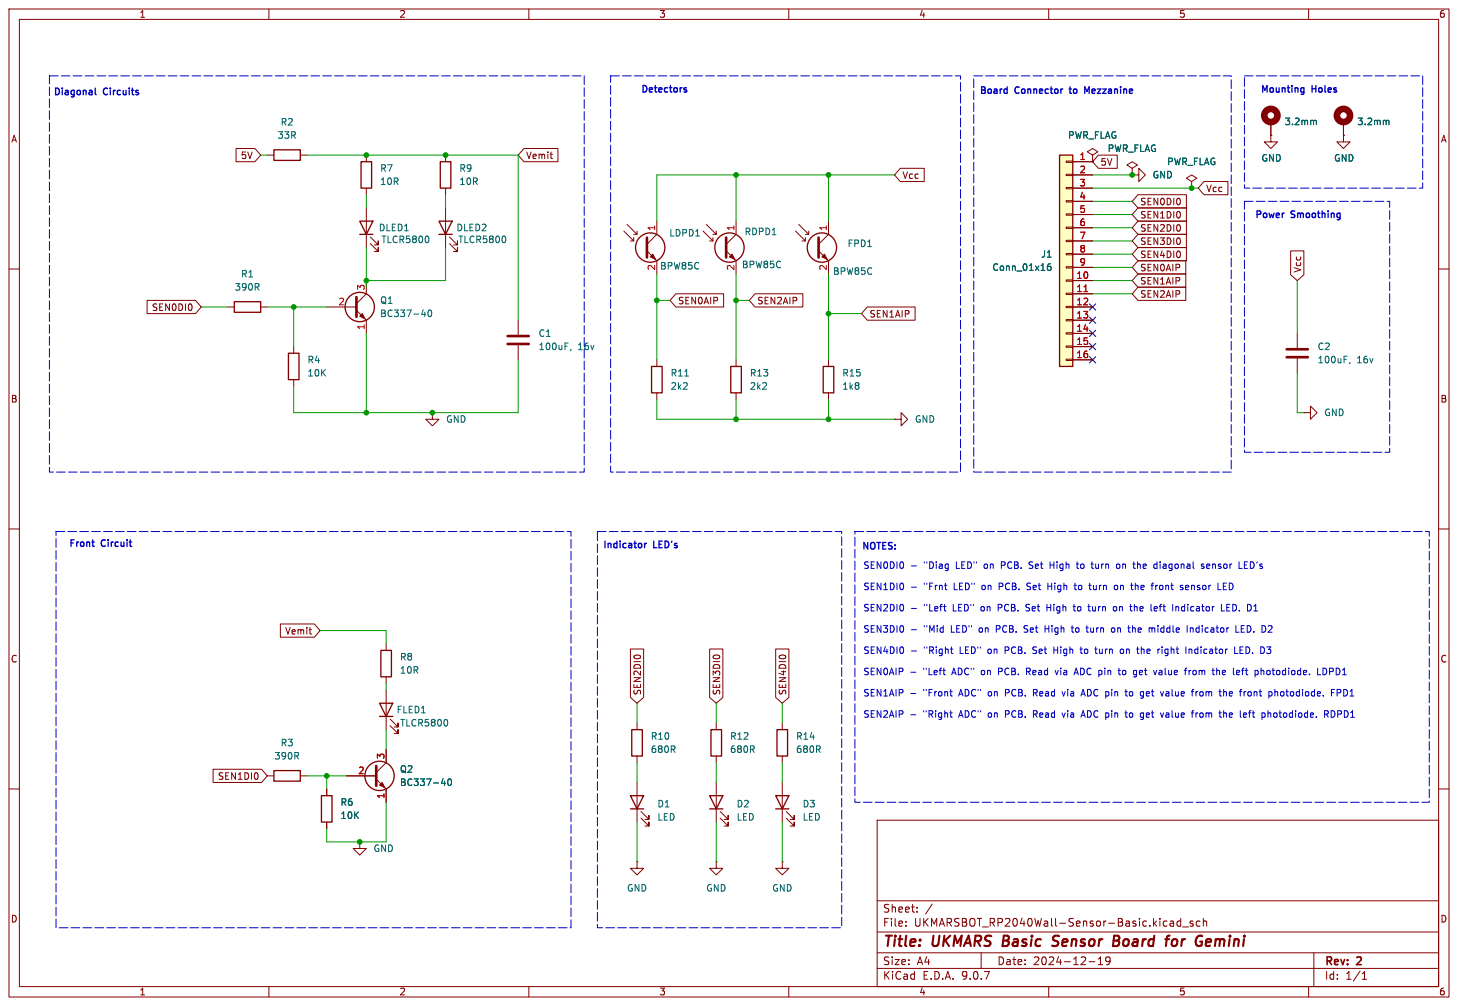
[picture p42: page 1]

Id: 1/1 Title: UKMARS Basic Sensor Board for Gemini File: UKMARSBOT_RP2040Wall-Sensor-Basic.kicad_sch Sheet: /

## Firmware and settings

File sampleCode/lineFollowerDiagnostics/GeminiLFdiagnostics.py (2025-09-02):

# Diagnostic code to verify the correct build of a UKMARS Gemini platform with line follower sensor using Pi Pico
# Updated for V2 board configuration
#
#Author:	Ian Butterworth
#Created:	29 April 2025
#Updated:	11 August 2025
#
#Connecting an HC05/HC06 bluetooth module to J2 on the mezzanine processor board will provide wireless reporting
#of the values measured to a serial monitor eg Putty or mobile phone
#
#The test phases are:
#
#0- flash the onboard LED							when done press the left button SW1
#1- flash the Gemini indicators and emitters		when done press the right button SW2
#2- read and display the sensor values				when done press the left button SW1
#3- read and display the encoder values				when done press the right button SW2
#4- move the robot forwards then backwards			automatically returns to test phase 0
#
#This programm requires diagnosticEncoders.py
#------------
#MIT License

#Copyright (c) 2025 Ian Butterworth

#Permission is hereby granted, free of charge, to any person obtaining a copy
#of this software and associated documentation files (the "Software"), to deal
#in the Software without restriction, including without limitation the rights
#to use, copy, modify, merge, publish, distribute, sublicense, and/or sell
#copies of the Software, and to permit persons to whom the Software is
#furnished to do so, subject to the following conditions:

#The above copyright notice and this permission notice shall be included in all
#copies or substantial portions of the Software.

#THE SOFTWARE IS PROVIDED "AS IS", WITHOUT WARRANTY OF ANY KIND, EXPRESS OR
#IMPLIED, INCLUDING BUT NOT LIMITED TO THE WARRANTIES OF MERCHANTABILITY,
#FITNESS FOR A PARTICULAR PURPOSE AND NONINFRINGEMENT. IN NO EVENT SHALL THE
#AUTHORS OR COPYRIGHT HOLDERS BE LIABLE FOR ANY CLAIM, DAMAGES OR OTHER
#LIABILITY, WHETHER IN AN ACTION OF CONTRACT, TORT OR OTHERWISE, ARISING FROM,
#OUT OF OR IN CONNECTION WITH THE SOFTWARE OR THE USE OR OTHER DEALINGS IN THE
#SOFTWARE.

from machine import Pin,ADC,PWM
import time
from diagnosticEncoders import Encoders
import os
from machine import UART
uart=UART(0, 115200)	#Select baudrate for bluetooth connection

leftsensor  = ADC(28)
rightsensor = ADC(26)
radiussensor = ADC(27)
startsensor = ADC(27)
emitter = Pin(22,Pin.OUT)
radiusEmitter = Pin(18,Pin.OUT)

onBoardLED = Pin("LED", Pin.OUT)
leftRedLED = Pin(21,Pin.OUT)		#Sensor
centreAmberLED = Pin(20,Pin.OUT)	#Sensor
rightGreenLED = Pin(19,Pin.OUT)	#Sensor
leftWhiteLED = Pin(12,Pin.OUT)	#Mezz
rightBlueLED = Pin(13,Pin.OUT)	#Mezz

leftRev = PWM(Pin(3))
leftRev.freq(2000)
leftFwd = PWM(Pin(2))
leftFwd.freq(2000)
rightRev = PWM(Pin(5))
rightRev.freq(2000)
rightFwd = PWM(Pin(4))
rightFwd.freq(2000)
leftButton = Pin(15, Pin.IN, Pin.PULL_UP)
rightButton = Pin(14, Pin.IN, Pin.PULL_UP)
encoders = Encoders()
#leftQuadA = Pin(9,Pin.IN)	#Not needed, pins are assigned in the encoders object
#leftQuadB = Pin(8,Pin.IN)
#rightQuadA = Pin(7,Pin.IN)
#rightQuadB = Pin(6,Pin.IN)

#Global variables to make readings available after the update function has run
leftSensorUnlit = 0
rightSensorUnlit = 0
radiusSensorUnlit = 0
startSensorUnlit =0
leftSensorValue = 0
rightSensorValue = 0
radiusSensorValue = 0
startSensorValue =0


def readSensors():
    #Values are derived by subtracting the lit value of a sensor from the unlit value and dividing by 512
    #to give a value in the range 0-127.
    #Unlit raw readings close to 65000 indicate good separation from ambient light
    #The variable detectedValue controls the illumination of inicator LEDs or each of the sensors so moving
    #the robot around over lines and markers will show detection
    #The radius and start/finish sensors are multiplexed onto the same ADC channel using separate emitters
    
    global leftSensorValue, rightSensorValue, radiusSensorValue, startSensorValue
    global leftSensorUnlit, rightSensorUnlit, radiusSensorUnlit, startSensorUnlit
    detectedValue = 64	#50% of saturated brightness
    emitter.value(0)
    radiusEmitter.value(0)
    leftSensorUnlit = leftsensor.read_u16()
    rightSensorUnlit = rightsensor.read_u16()
    startSensorUnlit = startsensor.read_u16()
    radiusSensorUnlit = radiussensor.read_u16()
    
    emitter.value(1)
    time.sleep_us(15)
    leftSensorLit = leftsensor.read_u16()
    rightSensorLit = rightsensor.read_u16()
    startSensorLit = startsensor.read_u16()
    emitter.value(0)
    
    radiusEmitter.value(1)
    time.sleep_us(15)
    radiusSensorLit = radiussensor.read_u16()
    radiusEmitter.value(0)
    
    leftSensorValue = (leftSensorUnlit - leftSensorLit) // 512	# limits range to 127
    rightSensorValue = (rightSensorUnlit - rightSensorLit) //512
    startSensorValue = (startSensorUnlit - startSensorLit) //512
    radiusSensorValue = (radiusSensorUnlit - radiusSensorLit) //512
    
    if leftSensorValue > detectedValue:
        leftRedLED.value(1)
    else:
        leftRedLED.value(0)
    if rightSensorValue > detectedValue:
        rightGreenLED.value(1)
    else:
        rightGreenLED.value(0)
    if startSensorValue > detectedValue:
        rightBlueLED.value(1)
    else:
        rightBlueLED.value(0)
    if radiusSensorValue > detectedValue:
        leftWhiteLED.value(1)
    else:
        leftWhiteLED.value(0)


#Set the motor pwm duty cycle from required speed expressed as a percentage 0-100
def leftMotor(speed):
    if speed < 0:
        speed = -speed
        if speed > 100:
            speed = 100
        dutyCycle = speed * 655
        leftFwd.duty_u16(0)
        leftRev.duty_u16(int(dutyCycle))
    else:
        if speed > 100:
            speed = 100
        dutyCycle = speed * 655
        leftRev.duty_u16(0)
        leftFwd.duty_u16(int(dutyCycle))

def rightMotor(speed):
    if speed < 0:
        speed = -speed
        if speed > 100:
            speed = 100
        dutyCycle = speed * 655
        rightFwd.duty_u16(0)
        rightRev.duty_u16(int(dutyCycle))
    else:
        if speed > 100:
            speed = 100
        dutyCycle = speed * 655
        rightRev.duty_u16(0)
        rightFwd.duty_u16(int(dutyCycle))

def stopMotors():       
    rightRev.duty_u16(0)
    rightFwd.duty_u16(0)
    leftRev.duty_u16(0)
    leftFwd.duty_u16(0)
    

def sequenceLEDs():
    #Cycle round flashing all the indicator LEDs and the emitters in turn
    #The emitters are pulsed as they are overdriven on a duty cycle
    period_ms = 200
    leftRedLED.value(1)
    time.sleep_ms(period_ms)
    leftRedLED.value(0)
    centreAmberLED.value(1)
    time.sleep_ms(period_ms)
    centreAmberLED.value(0)
    rightGreenLED.value(1)
    time.sleep_ms(period_ms)
    rightGreenLED.value(0)
    leftWhiteLED.value(1)
    time.sleep_ms(period_ms)
    leftWhiteLED.value(0)
    rightBlueLED.value(1)
    time.sleep_ms(period_ms)
    rightBlueLED.value(0)
    for pulses in range(0,40):
        emitter.value(1)
        time.sleep_us(15)
        emitter.value(0)
        time.sleep_ms(2)
    time.sleep_ms(period_ms)
    for pulses in range(0,40):
        radiusEmitter.value(1)
        time.sleep_us(15)
        radiusEmitter.value(0)
        time.sleep_ms(2)
    time.sleep_ms(period_ms)
    
def allOff():
    emitter.value(0)
    radiusEmitter.value(0)
    leftRedLED.value(0)
    centreAmberLED.value(0)
    rightGreenLED.value(0)
    leftWhiteLED.value(0)
    rightBlueLED.value(0)

#............................................
#
#Main Program starts here
#
stopMotors()
emitter.value(0)
radiusEmitter.value(0)
displayCount = 500
leftCount = 0
rightCount = 0
diagnosticLoopCount = 0

while True:
#Flash the on board LED until the left button is pressed
#This is a good time to establish a serial connection if using an HC05/06 bluetooth module
    while(leftButton.value() == 1):
        onBoardLED.value(1)
        time.sleep(0.1)
        onBoardLED.value(0)
        time.sleep(0.1)
    if diagnosticLoopCount == 0:
        uart.write('Hello\n\r')
        print('Hello')
    else:
        uart.write('Hello again\n\r')
        print('Hello again')
    diagnosticLoopCount += 1

#Now flash the Gemini LEDs and emitters until the right button is pressed
    while(rightButton.value() == 1):
        sequenceLEDs()
    allOff()
    
#Now read and display the sensors until the left button is pressed
    while(leftButton.value() == 1):
        readSensors()
        displayCount += 1
        if displayCount > 500:
            print(radiusSensorUnlit,leftSensorUnlit,rightSensorUnlit,startSensorUnlit,radiusSensorValue,leftSensorValue,rightSensorValue,startSensorValue)
            uart.write(str(radiusSensorUnlit))
            uart.write('    ')
            uart.write(str(leftSensorUnlit))
            uart.write('    ')
            uart.write(str(rightSensorUnlit))
            uart.write('    ')
            uart.write(str(startSensorUnlit))
            uart.write('    ')
            uart.write(str(radiusSensorValue))
            uart.write('    ')
            uart.write(str(leftSensorValue))
            uart.write('    ')
            uart.write(str(rightSensorValue))
            uart.write('    ')
            uart.write(str(startSensorValue))
            uart.write(chr(10))
            uart.write(chr(13))
            displayCount = 0
        time.sleep_ms(2)
    allOff()
    
#Now read and display the encoders until the right button is pressed
    displayCount = 500
    leftCount, rightCount = encoders.get_counts(True)
    while(rightButton.value() == 1):
        leftCount, rightCount = encoders.get_counts(False)
        displayCount += 1
        if displayCount > 500:
            print(leftCount,rightCount)
            uart.write(str(leftCount))
            uart.write('    ')
            uart.write(str(rightCount))
            uart.write(chr(10))
            uart.write(chr(13))
            displayCount = 0
        time.sleep_ms(2)


#Now move the robot forwards then backwards
#If the robot is only being powered by the USB connector lift it off the surface to allow the motors to work!
    rightMotor(35)
    leftMotor(35)
    time.sleep_ms(500)
    stopMotors()
    time.sleep_ms(500)
    rightMotor(-35)
    leftMotor(-35)
    time.sleep_ms(500)
    stopMotors()
    time.sleep_ms(500)

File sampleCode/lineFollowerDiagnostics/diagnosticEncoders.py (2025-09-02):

#Very simple encoder class to return counts to the line follower diagnostic program
#Uses a quadrature encoder counter implemented in PIO from:
#https://github.com/raspberrypi/pico-examples/blob/master/pio/quadrature_encoder/quadrature_encoder.pio
#Encoder pin assignments and rotataion directions are hard coded in the class definition
#
#
# type: ignore

import machine
import utime
import rp2
from machine import Pin
import array

class PIOQuadratureCounter:
    
    @rp2.asm_pio(autopush=False, autopull=False)
    
    def counter():
        jmp("update")    # 00 -> 00
        jmp("decrement") # 00 -> 01
        jmp("increment") # 00 -> 10
        jmp("update")    # 00 -> 11
        
        jmp("increment") # 01 -> 00
        jmp("update")    # 01 -> 01
        jmp("update")    # 01 -> 10
        jmp("decrement") # 01 -> 11
        
        jmp("decrement") # 10 -> 00
        jmp("update")    # 10 -> 01
        jmp("update")    # 10 -> 10
        jmp("increment") # 10 -> 11
        
        jmp("update")    # 11 -> 00
        jmp("increment") # 11 -> 01
        label("decrement")#11 -> 10
        jmp(y_dec, "update")
        label("update")  # 11 -> 11
        
        wrap_target()
        set(x, 0)
        pull(noblock) # check for request
        
        mov(x, osr)
        mov(osr, isr) # OSR = previous pins
        jmp(not_x, "sample_pins")
        
        # report data
        mov(isr, y)
        push()
        
        label("sample_pins")
        mov(isr, null)
        in_(osr, 2)
        in_(pins, 2)
        mov(pc, isr) # jump to <previous>:<current>
        
        label("increment")
        mov(x, invert(y))
        jmp(x_dec, "increment2")
        label("increment2")
        mov(y, invert(x))
        wrap()
        nop() # We have to fill up the program space or Micropython won't put it at the
        nop() # beginning of the program, and the jump table doesn't work.
        nop()

    def __init__(self, pio1, pin1, pin2):
        if pin2 != pin1 + 1:
            raise Exception("pin2 must be pin1 + 1")
        
        Pin(pin1, Pin.IN, Pin.PULL_UP)
        Pin(pin2, Pin.IN, Pin.PULL_UP)
        self.sm1 = rp2.StateMachine(pio1, self.counter, freq=125000000, in_base=machine.Pin(pin1))
        self.sm1.active(1)
        self.buf = array.array('i', [0])
    
    def read(self):
        self.sm1.put(1)

        # For efficiency, here we use an undocumented feature of
        # StateMachine to read a SIGNED integer value without
        # allocating a new object.
        self.sm1.get(self.buf)
        return self.buf[0]


class Encoders:
    def __init__(self):
        self.left = PIOQuadratureCounter(0, 8, 9)
        self.right = PIOQuadratureCounter(1, 6, 7)

        # Zero counts
        self.left_offset = 0
        self.right_offset = 0
        self.get_counts(reset = True)

    def get_counts(self, reset = False):
        # Sign on left encoders is reversed from what
        # the PIO counter gives us.
        left = -self.left.read() - self.left_offset
        right = self.right.read() - self.right_offset

        if reset:
            self.left_offset += left
            self.right_offset += right

        return left , right

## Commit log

2025-01-08 Added ignore for kicad files
2025-01-14 Original Pico Bot solution design
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2025-01-25 Update Requirements.md
    Added motor choice
2025-01-26 add files for Pololu wheels
    [pololu-wheel-32x7mm-black.step, pololu-wheel-32x7mm-white.step]
2025-01-26 adds some connector datasheets
2025-01-26 adds some RP2040 datasheets
    [MAKER-NANO-RP2040.STEP]
2025-01-26 add Pico-W STEP file
    [RP2040-PICO-W.stp]
2025-01-26 add pico-w pinout diagram
2025-01-27 add datasheet for HR8833 motor driver
2025-01-29 add motor mount and riser
    [motor-bracket.stl, motor-riser-5mm.stl]
2025-02-02 Battery and RP2040 Connect model
    [Battery_9V.STEP, Nano_RP2040_Connect v1.step]
2025-02-05 Update Requirements.md
    Fix reference to wrong Pololu encoder set and update decision of initial mezzanine board
2025-02-11 Update Requirements.md
    Confirm choice of wheels and tyres
2025-02-15 Added board connections from closed issue #17
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2025-02-16 First checkin on Chassis Kicad files. Need to confirm location for mezz connectors. Silkscreen is not complete. Not happy with the motor voltage selector location.
    [UKMARSBOT_RP2040Chassis.kicad_pcb, UKMARSBOT_RP2040Chassis.kicad_sch]
2025-02-16 fixed ignore file. Libraries from previous project. A verison of chassis, mezzanine and sensor board. Needed to play with connector locations. Nothing completly finished but i think the chassis and m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
    [UKMARSBOT_RP2040Mezzanine.kicad_pcb, UKMARSBOT_RP2040Mezzanine.kicad_sch, UKMARSBOT_v2_wall-sensor-basic.kicad_pcb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]
2025-02-16 Rename to have some consistancy
    [UKMARSBOT_RP2040Wall-Sensor-Basic.kicad_pcb, UKMARSBOT_RP2040Wall-Sensor-Basic.kicad_sch]
2025-02-17 Update to 5v rail and layouts across all 3 boards
    [UKMARSBOT_RP2040Chassis.kicad_pcb, UKMARSBOT_RP2040Chassis.kicad_sch, UKMARSBOT_RP2040Mezzanine.kicad_pcb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]
2025-02-28 Update to schematic to fix copy and paste error and add in a new indicator LED. Tidied up schematic to be more readable
    [UKMARSBOT_RP2040Wall-Sensor-Basic.kicad_sch]
2025-02-28 Flush mount resistors and diodes
    [UKMARSBOT_RP2040Chassis.kicad_sch, UKMARSBOT_RP2040Mezzanine.kicad_sch, UKMARSBOT_RP2040Wall-Sensor-Basic.kicad_pcb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]
2025-02-28 Capacitor smoothing. Chassis placement changes, Mez board made smaller and added an additional LED
    [UKMARSBOT_RP2040Chassis.kicad_pcb, UKMARSBOT_RP2040Chassis.kicad_sch, UKMARSBOT_RP2040Mezzanine.kicad_pcb]
2025-03-06 First draft Line Sensor Basic pcb
    First design of a sensor board for 1/2 size line following observing the restriction of only 3 A/D channels being available
    [UKMARSBOT_LineSensorBasic.kicad_pcb, UKMARSBOT_LineSensorBasic.kicad_sch]
2025-03-07 Connectors moved to be on common 0.1" Grid and wheel cutouts included
    [UKMARSBOT_LineSensorBasic.kicad_pcb, UKMARSBOT_RP2040Chassis.kicad_pcb, UKMARSBOT_RP2040Mezzanine.kicad_pcb]
2025-03-08 Create DRV8833.md
    Notes about the motor drivers
2025-03-08 Basic line sensor modified for new connector position
    [UKMARSBOT_LineSensorBasic.kicad_pcb, UKMARSBOT_LineSensorBasic.kicad_sch]
2025-03-09 Routed Chassis board with sleep pullup on motor bridge
    [UKMARSBOT_RP2040Chassis.kicad_pcb, UKMARSBOT_RP2040Chassis.kicad_sch]
2025-03-09 Updates components based on issues #27 and #28 Placement and routing of PCB has been done
    [UKMARSBOT_RP2040Wall-Sensor-Basic.kicad_pcb, UKMARSBOT_RP2040Wall-Sensor-Basic.kicad_sch]
2025-03-09 Updated silkscreen on wall sensor
    [UKMARSBOT_RP2040Wall-Sensor-Basic.kicad_pcb]
2025-03-11 Routed Chassis and Mezzanine Boards
    Position and orientate motor connections to allow use of JST-SH breakout connectors. Position and orientate spare pin breakout to accomodate bluetooth module. Re-assign pins and orientate Pico to fac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
    [UKMARSBOT_RP2040Chassis.kicad_pcb, UKMARSBOT_RP2040Chassis.kicad_sch, UKMARSBOT_RP2040Mezzanine.kicad_pcb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]
2025-03-13 Updates to wall sensor based on feedback
    [UKMARSBOT_RP2040Wall-Sensor-Basic.kicad_pcb, UKMARSBOT_RP2040Wall-Sensor-Basic.kicad_sch]
2025-03-14 Added notes to link schematic tags to PCB silkscreen
    [UKMARSBOT_RP2040Wall-Sensor-Basic.kicad_sch]
2025-03-16 Updated Chassis and Mezzanine board - Sensor boards need to reflect new connector position
    [UKMARSBOT_RP2040Chassis.kicad_pcb, UKMARSBOT_RP2040Chassis.kicad_sch, UKMARSBOT_RP2040Mezzanine.kicad_pcb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]
2025-03-17 Position sensor slot layer correctly
    [UKMARSBOT_RP2040Mezzanine.kicad_pcb]
2025-03-17 Revised lime sensor board and sensor mounting hole moved forward 1.27mm for connector
    [UKMARSBOT_LineSensorBasic.kicad_pcb, UKMARSBOT_LineSensorBasic.kicad_sch, UKMARSBOT_RP2040Chassis.kicad_pcb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]
2025-03-19 Revised Wall Sensor Board consistent with hole and connector position. Fabrication files created.
    [UKMARSBOT_LineSensorBasic-B_Cu.gbr, UKMARSBOT_LineSensorBasic-B_Mask.gbr, UKMARSBOT_LineSensorBasic-B_Paste.gbr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]
2025-04-07 Title was wrong on the plot. Text updated to be accurate. No change to the design
    [UKMARSBOT_RP2040Wall-Sensor-Basic.kicad_sch]
2025-04-09 Fixed an issue with the transistor schematic being wrong for the wall sensor board.
    [UKMARSBOT_RP2040Wall-Sensor-Basic.kicad_pcb, UKMARSBOT_RP2040Wall-Sensor-Basic.kicad_sch]
2025-04-30 Diagnostic code to verify correct build of a line follower robot
    [GeminiLFdiagnostics.py, diagnosticEncoders.py]
2025-05-01 Modified to work with pico and pico W
2025-05-29 Create geminiBasicLineFollower.py
    Add example code for a basic line follower using the basic line sensor board and correctly stopping at the end of a lap.
    [geminiBasicLineFollower.py]
2025-07-02 Reworked chassis board for production
    Board reworked based on known issues from prototype builds.
    [UKMARSBOT_LineSensorBasic.kicad_pcb, UKMARSBOT_LineSensorBasic.kicad_sch, UKMARSBOT_RP2040Chassis.kicad_pcb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]
2025-07-05 Updated Mezzanine for PiPico
    Updated for v2.0 board set addressing all issues raised on the prototype board.
    [UKMARSBOT_RP2040Mezzanine.kicad_pcb, UKMARSBOT_RP2040Mezzanine.kicad_sch]
2025-07-05 Updated basic line follower board
    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
    [UKMARSBOT_LineSensorBasic.kicad_pcb, UKMARSBOT_LineSensorBasic.kicad_sch]
2025-07-07 Add v2 wall sensor board
    Wall sensor updated for Issues raised on prototype builds. Better pin markings added to Line sensor, mezz and chassis boards
    [UKMARSBOT_LineSensorBasic.kicad_pcb, UKMARSBOT_LineSensorBasic.kicad_sch, UKMARSBOT_RP2040Chassis.kicad_pcb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]
2025-07-09 V2 boards as sent to fabrication
    [UKMARSBOT_LineSensorBasic-B_Cu.gbr, UKMARSBOT_LineSensorBasic-B_Mask.gbr, UKMARSBOT_LineSensorBasic-B_Paste.gbr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]
2025-07-09 Add table mapping Pico pins to devices and functions
    [GeminiV2PicoPins.xlsx]
2025-07-31 Update wall sensor board connector to socket and transistor base resistor values
    [UKMARSBOT_RP2040Wall-Sensor-Basic.kicad_pcb, UKMARSBOT_RP2040Wall-Sensor-Basic.kicad_sch]
2025-08-14 Merge V2.1 into main and tag as V2.1.0 (#80)
    * Fixed an issue with the transistor schematic being wrong for the wall sensor board.
    * Updated PDF's
    * Reworked chassis board for production
    * Updated Mezzanine for PiPico
    * Updated basic line follower board
    * Add v2 wall sensor board
    * V2 boards as sent to fabrication
    * Add table mapping Pico pi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
    [UKMARSBOT_LineSensorBasic.kicad_sch, UKMARSBOT_LineSensorBasic_bom.csv, UKMARSBOT_RP2040Chassis.kicad_pcb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]
2025-08-14 Added RAPID field to all files and updated automation to pull this new field into BOM files
    [UKMARSBOT_LineSensorBasic.kicad_sch, UKMARSBOT_RP2040Chassis.kicad_sch, UKMARSBOT_RP2040Mezzanine.kicad_sch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]
2025-08-14 docs: update KiCad exports [skip ci]
    [UKMARSBOT_LineSensorBasic_bom.csv, UKMARSBOT_RP2040Chassis_bom.csv, UKMARSBOT_RP2040Mezzanine_bom.csv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]
2025-08-16 V2.1 Boards ready for fabrication
    [UKMARSBOT_LineSensorBasic-B_Cu.gbr, UKMARSBOT_LineSensorBasic-B_Mask.gbr, UKMARSBOT_LineSensorBasic-B_Paste.gbr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]
2025-08-25 Adding 3D printable motor mount
    [GeminiN20MotorMount.stl]
2025-08-28 Updated readme to include non BOM parts
2025-08-29 Updated sample code for line follower and LF diagnostics
2025-08-31 Updated sample code from David
2025-09-02 revert sample code file name change
    [geminiBasicLineFollower.py]
2025-09-06 Fixed an incorrect RAPID code on the chassis board
    [UKMARSBOT_RP2040Chassis.kicad_sch]
2025-10-23 Correct C1 and C2 Rapid Component codes for 7805 regulator specified
    [UKMARSBOT_RP2040Chassis.kicad_sch]
